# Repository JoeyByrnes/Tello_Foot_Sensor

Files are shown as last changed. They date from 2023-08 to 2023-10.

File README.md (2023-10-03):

# Tello Foot Sensor
Design Files and Firmware for an Ankle Encoder + Loadcell Amplifier Combo PCB for Tello Bipedal Robot

- STM32G4 Collects sensor data and streams over CAN-FD
- Position and velocity of the AS5147U encoder is read and streamed at 1KHz
- Two loadcells are read through two ADS1220 amplifiers and streamed at 1KHz
  - Optionally, four loadcells can be connected and streamed at ~700Hz

<p align="center">
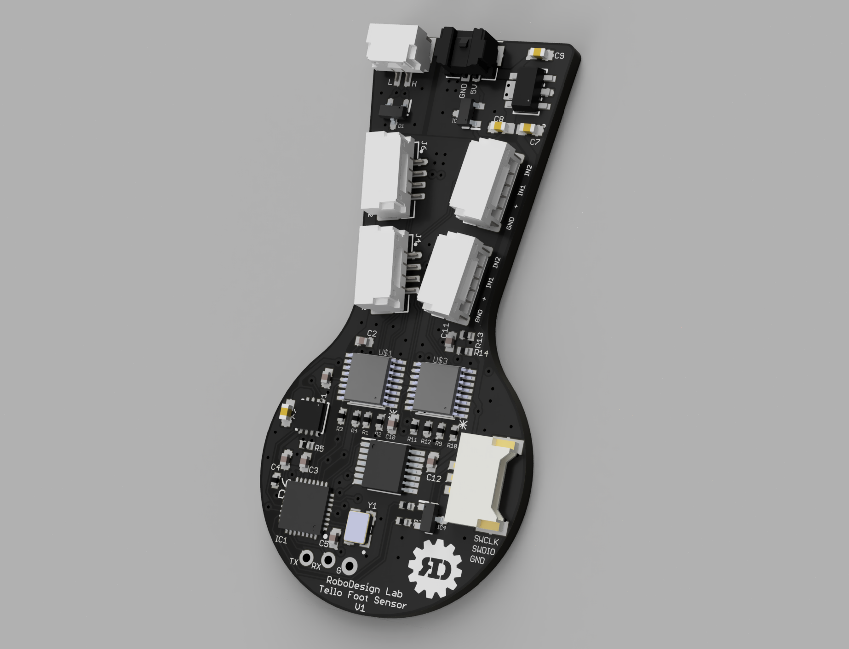
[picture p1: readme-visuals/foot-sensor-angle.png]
  
</p>
<p align="center">
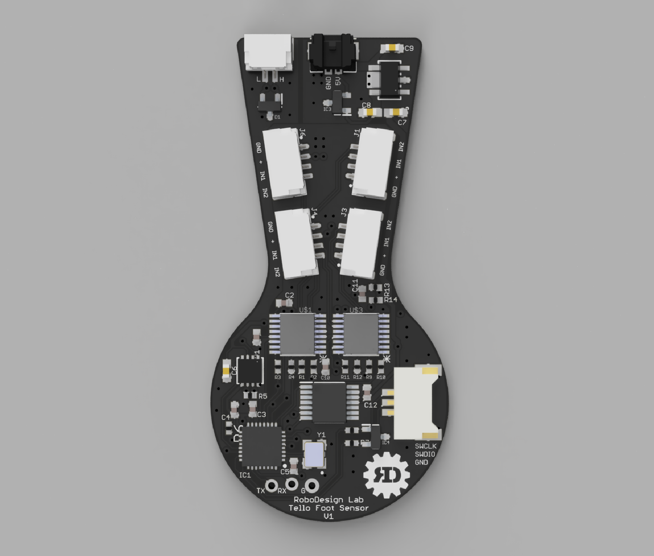
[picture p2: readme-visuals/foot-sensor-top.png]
  
</p>
<p align="center">
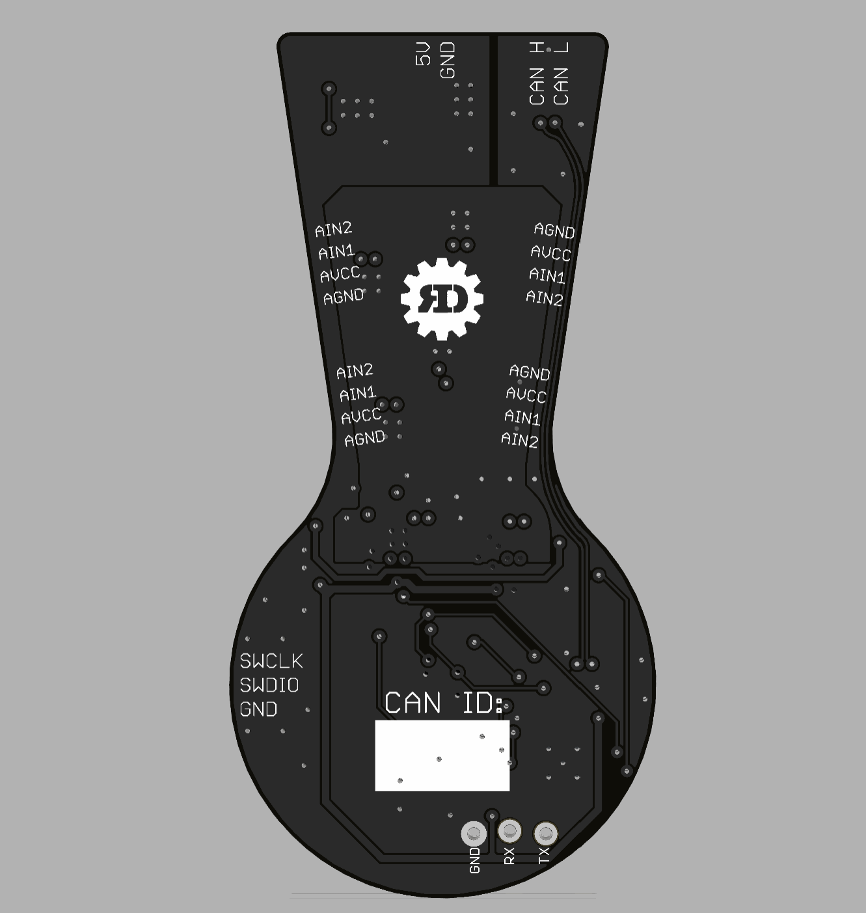
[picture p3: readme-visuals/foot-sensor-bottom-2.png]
  
</p>
<p align="center">
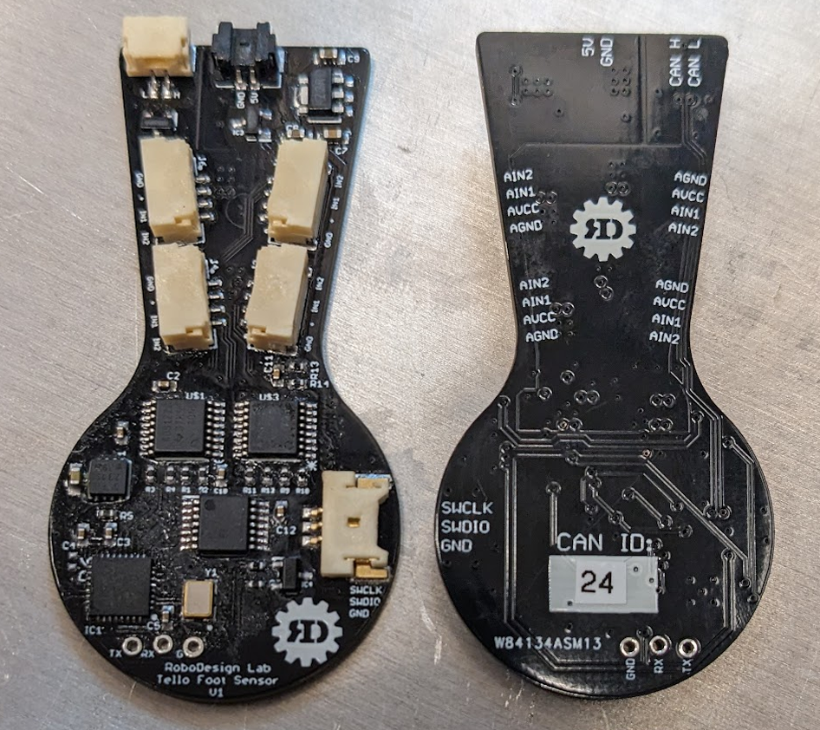
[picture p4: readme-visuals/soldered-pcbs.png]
  
</p>
<p align="center">
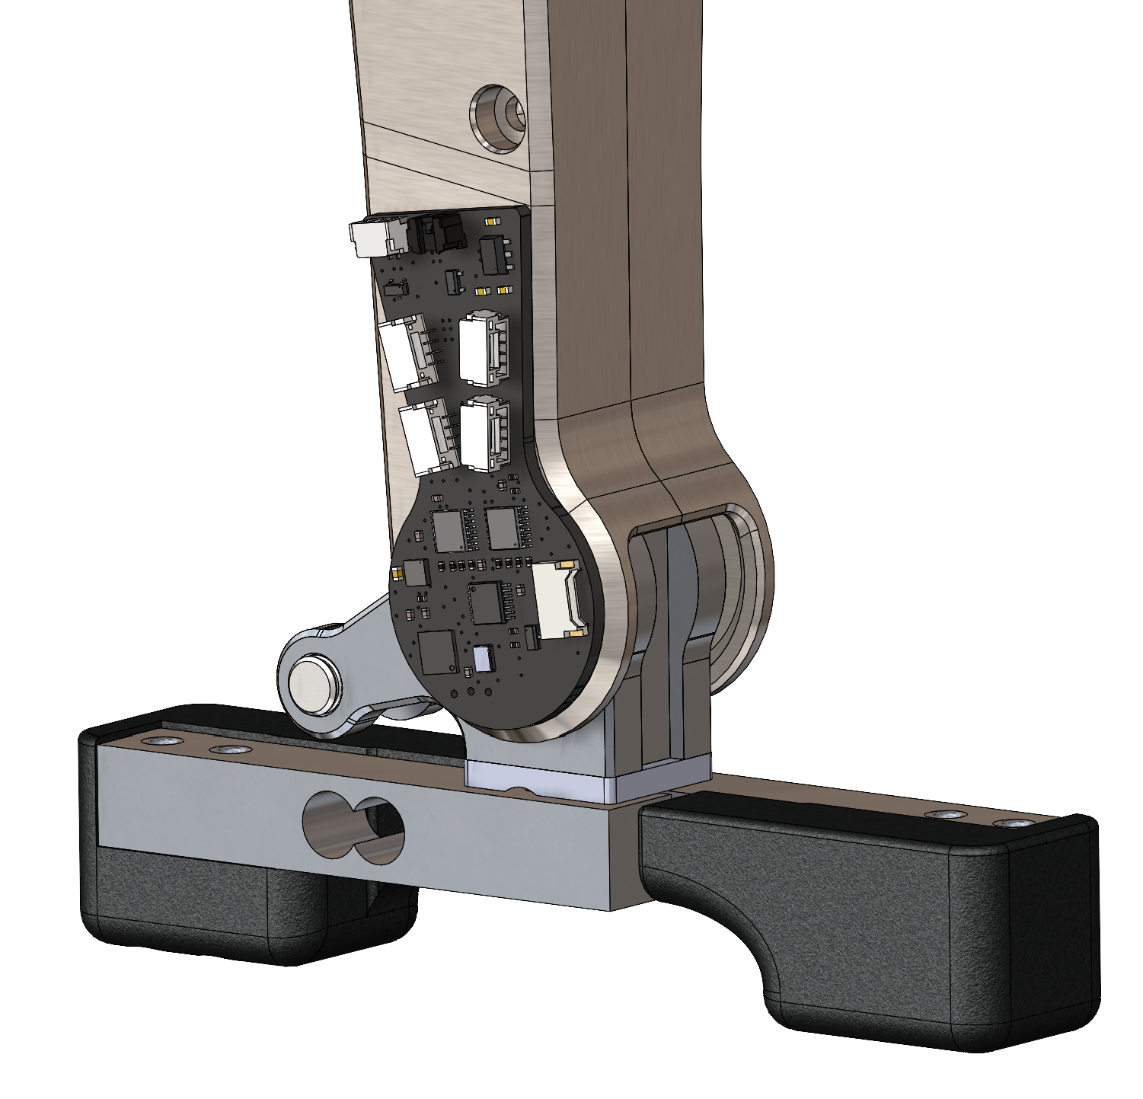
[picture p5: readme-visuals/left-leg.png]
  
</p>

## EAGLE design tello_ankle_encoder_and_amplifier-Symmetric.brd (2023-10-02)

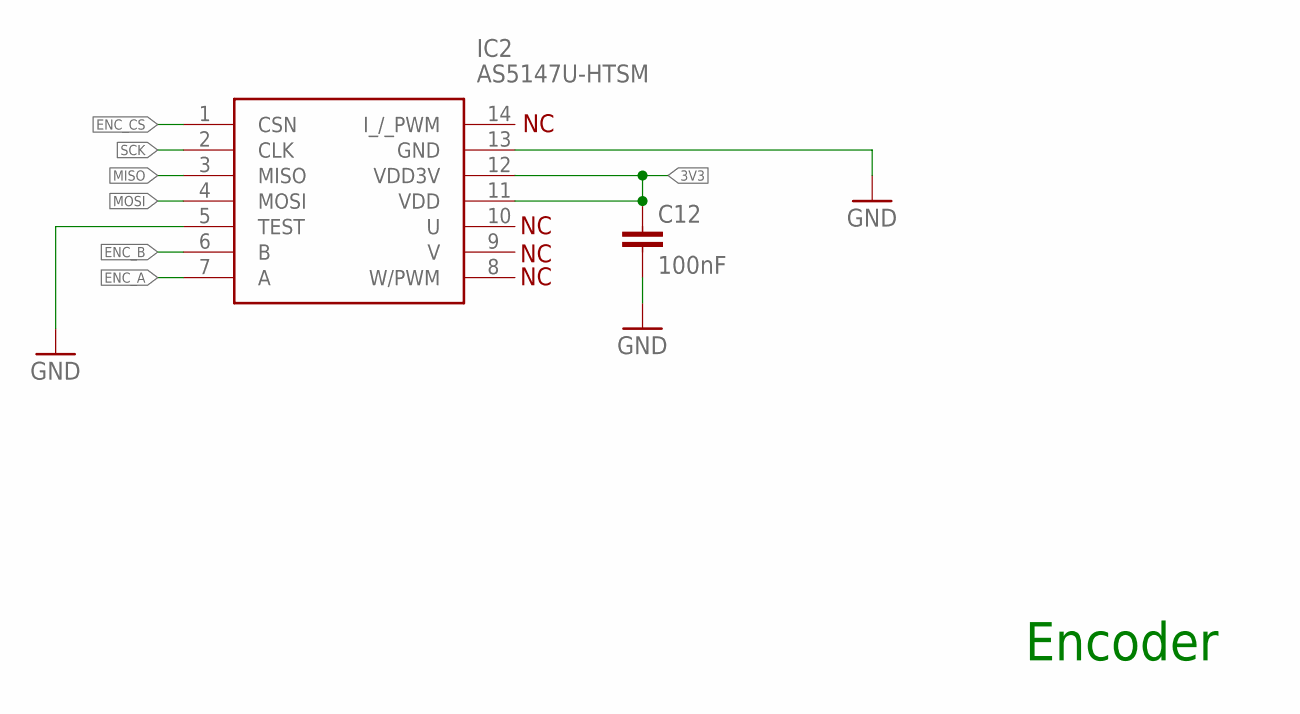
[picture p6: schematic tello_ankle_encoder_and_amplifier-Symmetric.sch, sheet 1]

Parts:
C12: 100nF; C0402
IC2: AS5147U-HTSM; SOP65P640X120-14N

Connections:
3V3: C12.1, IC2.11 (VDD), IC2.12 (VDD3V); also elsewhere on the board
ENC_A: IC2.7 (A); also elsewhere on the board
ENC_B: IC2.6 (B); also elsewhere on the board
ENC_CS: IC2.1 (CSN); also elsewhere on the board
GND: C12.2, IC2.5 (TEST), IC2.13 (GND); also elsewhere on the board
MISO: IC2.3 (MISO); also elsewhere on the board
MOSI: IC2.4 (MOSI); also elsewhere on the board
SCK: IC2.2 (CLK); also elsewhere on the board

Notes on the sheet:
Encoder

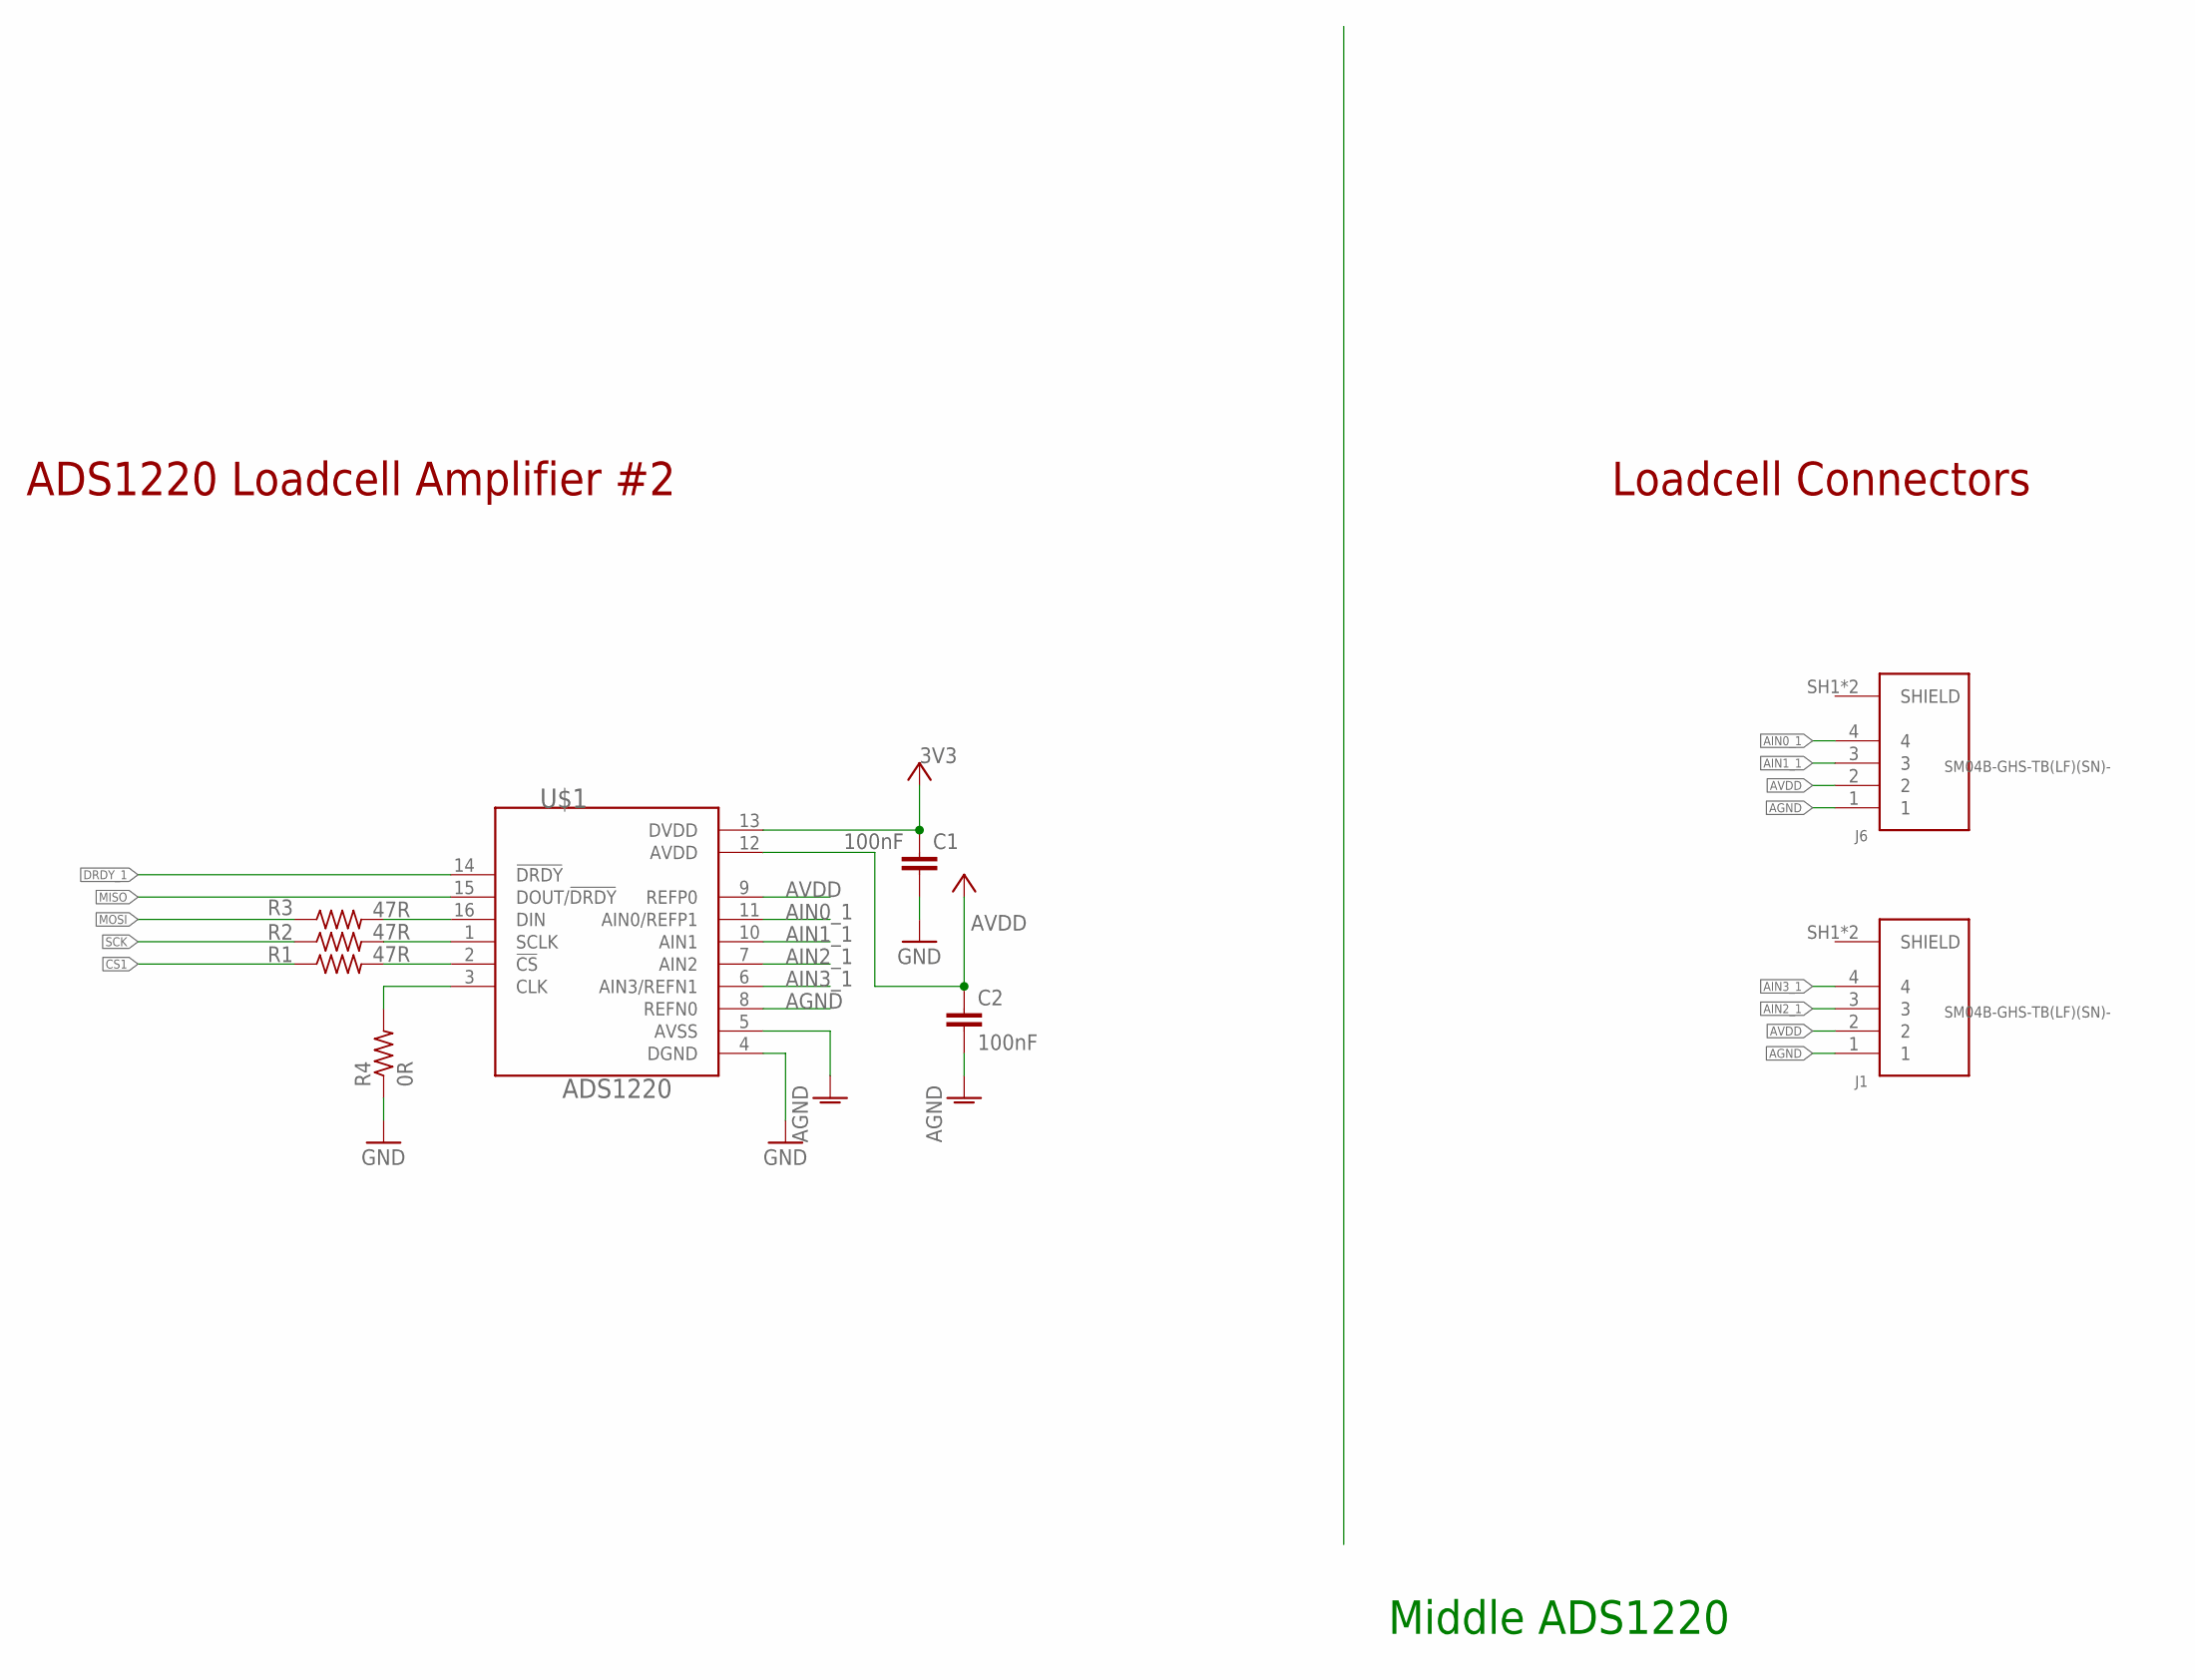
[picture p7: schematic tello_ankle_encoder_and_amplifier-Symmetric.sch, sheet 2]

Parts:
C1, C2: 100nF; C0402
J1, J6: SM04B-GHS-TB(LF)(SN)-; JST_SM04B-GHS-TB(LF)(SN)-
R1, R2, R3: 47R; R0402
R4: 0R; R0402
U$1: ADS1220; TSSOP-16

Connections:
3V3: C1.1, U$1.13 (DVDD); also elsewhere on the board
AGND: C2.2, J1.1, J6.1, U$1.5 (AVSS), U$1.8 (REFN0); also elsewhere on the board
AIN0_1: J6.4, U$1.11 (AIN0/REFP1)
AIN1_1: J6.3, U$1.10 (AIN1)
AIN2_1: J1.3, U$1.7 (AIN2)
AIN3_1: J1.4, U$1.6 (AIN3/REFN1)
AVDD: C2.1, J1.2, J6.2, U$1.9 (REFP0), U$1.12 (AVDD); also elsewhere on the board
CS1: R1.1; also elsewhere on the board
DRDY_1: U$1.14 (!DRDY); also elsewhere on the board
GND: C1.2, R4.1, U$1.4 (DGND); also elsewhere on the board
MISO: U$1.15 (DOUT/!DRDY); also elsewhere on the board
MOSI: R3.1; also elsewhere on the board
unnamed: R3.2, U$1.16 (DIN)
unnamed: R2.2, U$1.1 (SCLK)
unnamed: R1.2, U$1.2 (!CS)
unnamed: R4.2, U$1.3 (CLK)
SCK: R2.1; also elsewhere on the board
SHIELD: J1.SH1 (SHIELD), J1.SH2 (SHIELD), J6.SH1 (SHIELD), J6.SH2 (SHIELD); also elsewhere on the board

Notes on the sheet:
Middle ADS1220
ADS1220 Loadcell Amplifier #2
Loadcell Connectors

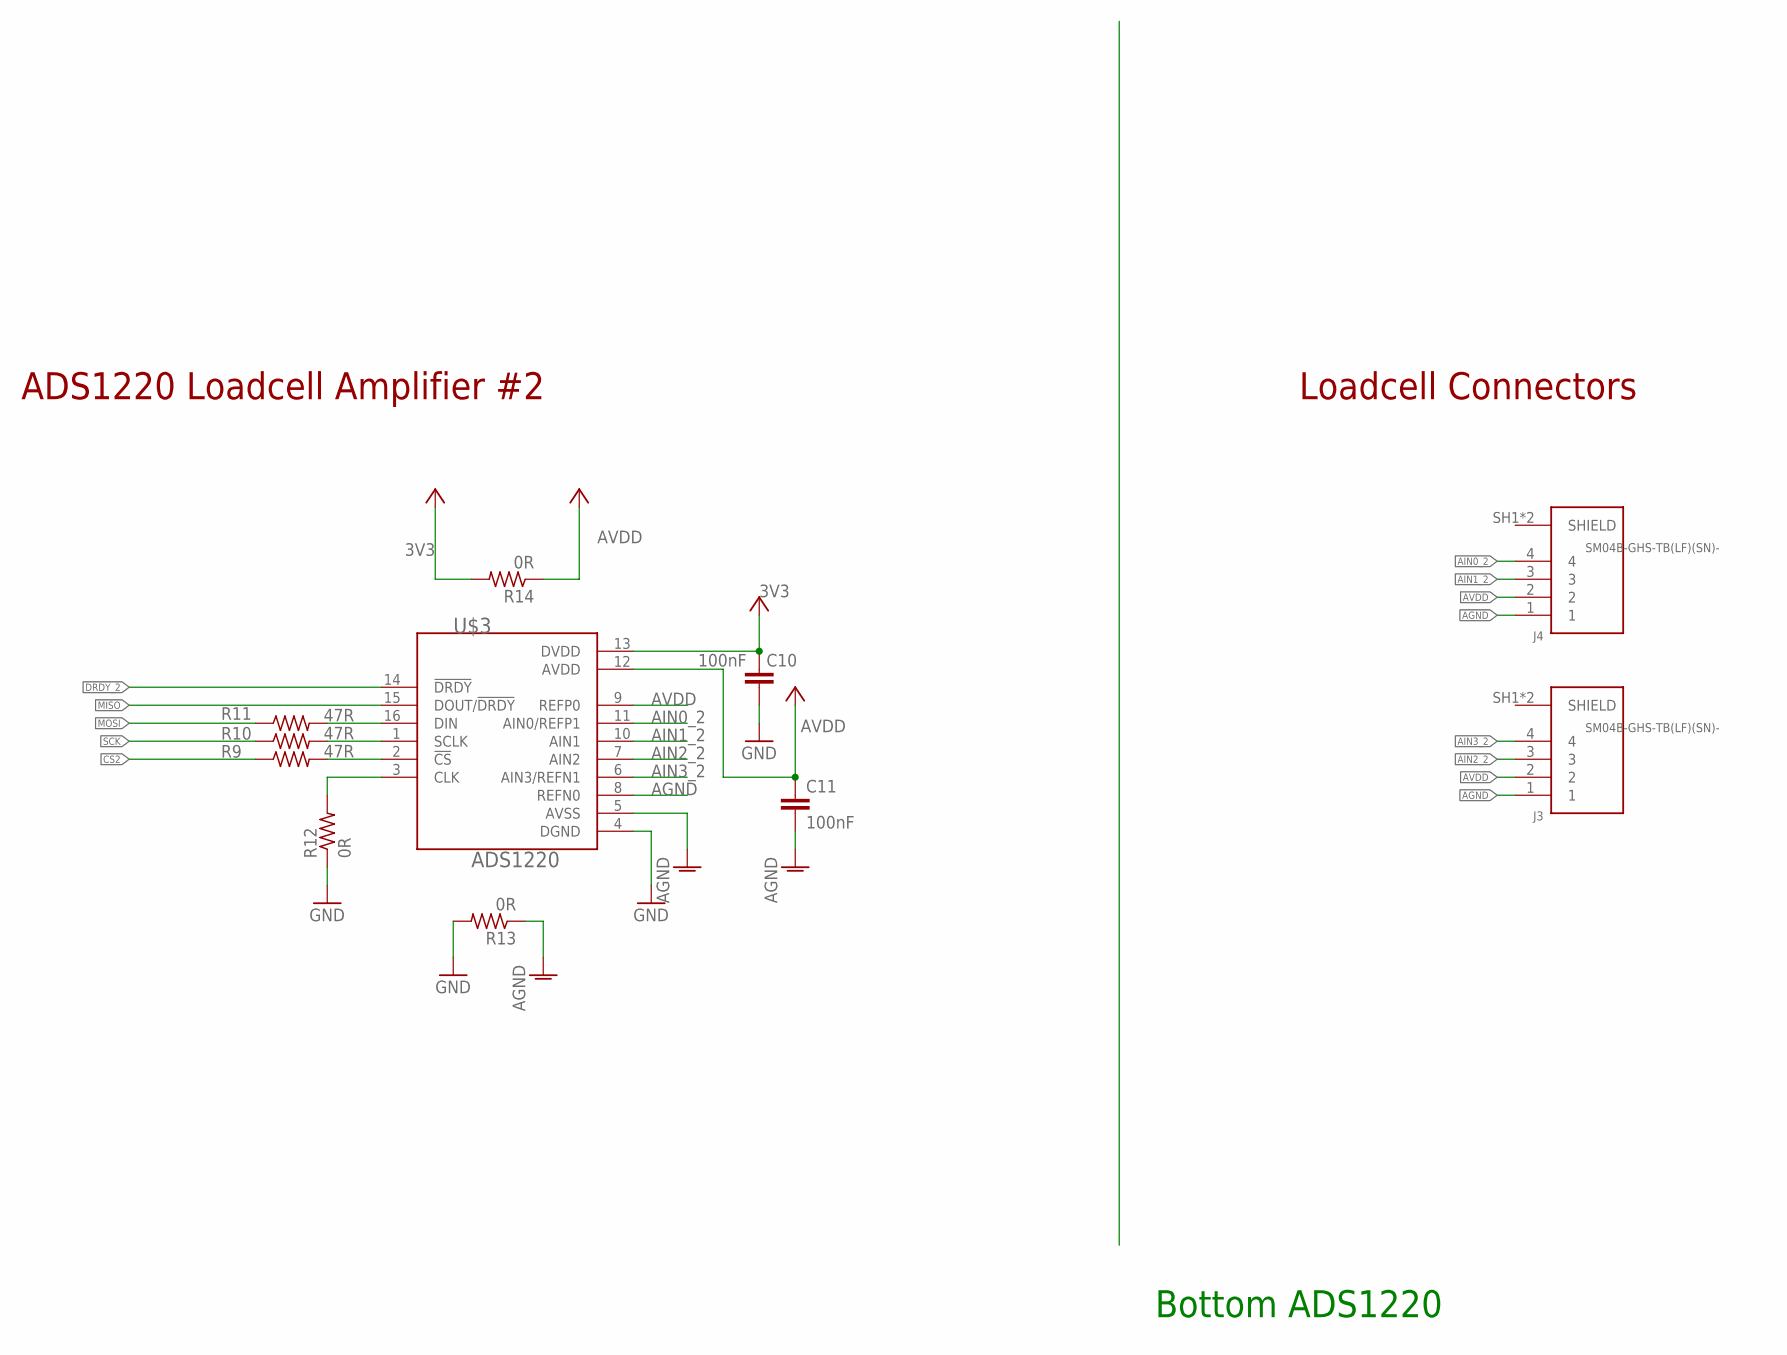
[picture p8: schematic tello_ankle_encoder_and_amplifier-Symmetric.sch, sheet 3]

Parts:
C10, C11: 100nF; C0402
J3, J4: SM04B-GHS-TB(LF)(SN)-; JST_SM04B-GHS-TB(LF)(SN)-
R9, R10, R11: 47R; R0402
R12, R13, R14: 0R; R0402
U$3: ADS1220; TSSOP-16

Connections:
3V3: C10.1, R14.2, U$3.13 (DVDD); also elsewhere on the board
AGND: C11.2, J3.1, J4.1, R13.1, U$3.5 (AVSS), U$3.8 (REFN0); also elsewhere on the board
AIN0_2: J4.4, U$3.11 (AIN0/REFP1)
AIN1_2: J4.3, U$3.10 (AIN1)
AIN2_2: J3.3, U$3.7 (AIN2)
AIN3_2: J3.4, U$3.6 (AIN3/REFN1)
AVDD: C11.1, J3.2, J4.2, R14.1, U$3.9 (REFP0), U$3.12 (AVDD); also elsewhere on the board
CS2: R9.1; also elsewhere on the board
DRDY_2: U$3.14 (!DRDY); also elsewhere on the board
GND: C10.2, R12.1, R13.2, U$3.4 (DGND); also elsewhere on the board
MISO: U$3.15 (DOUT/!DRDY); also elsewhere on the board
MOSI: R11.1; also elsewhere on the board
unnamed: R11.2, U$3.16 (DIN)
unnamed: R10.2, U$3.1 (SCLK)
unnamed: R9.2, U$3.2 (!CS)
unnamed: R12.2, U$3.3 (CLK)
SCK: R10.1; also elsewhere on the board
SHIELD: J3.SH1 (SHIELD), J3.SH2 (SHIELD), J4.SH1 (SHIELD), J4.SH2 (SHIELD); also elsewhere on the board

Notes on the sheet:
Bottom ADS1220
ADS1220 Loadcell Amplifier #2
Loadcell Connectors

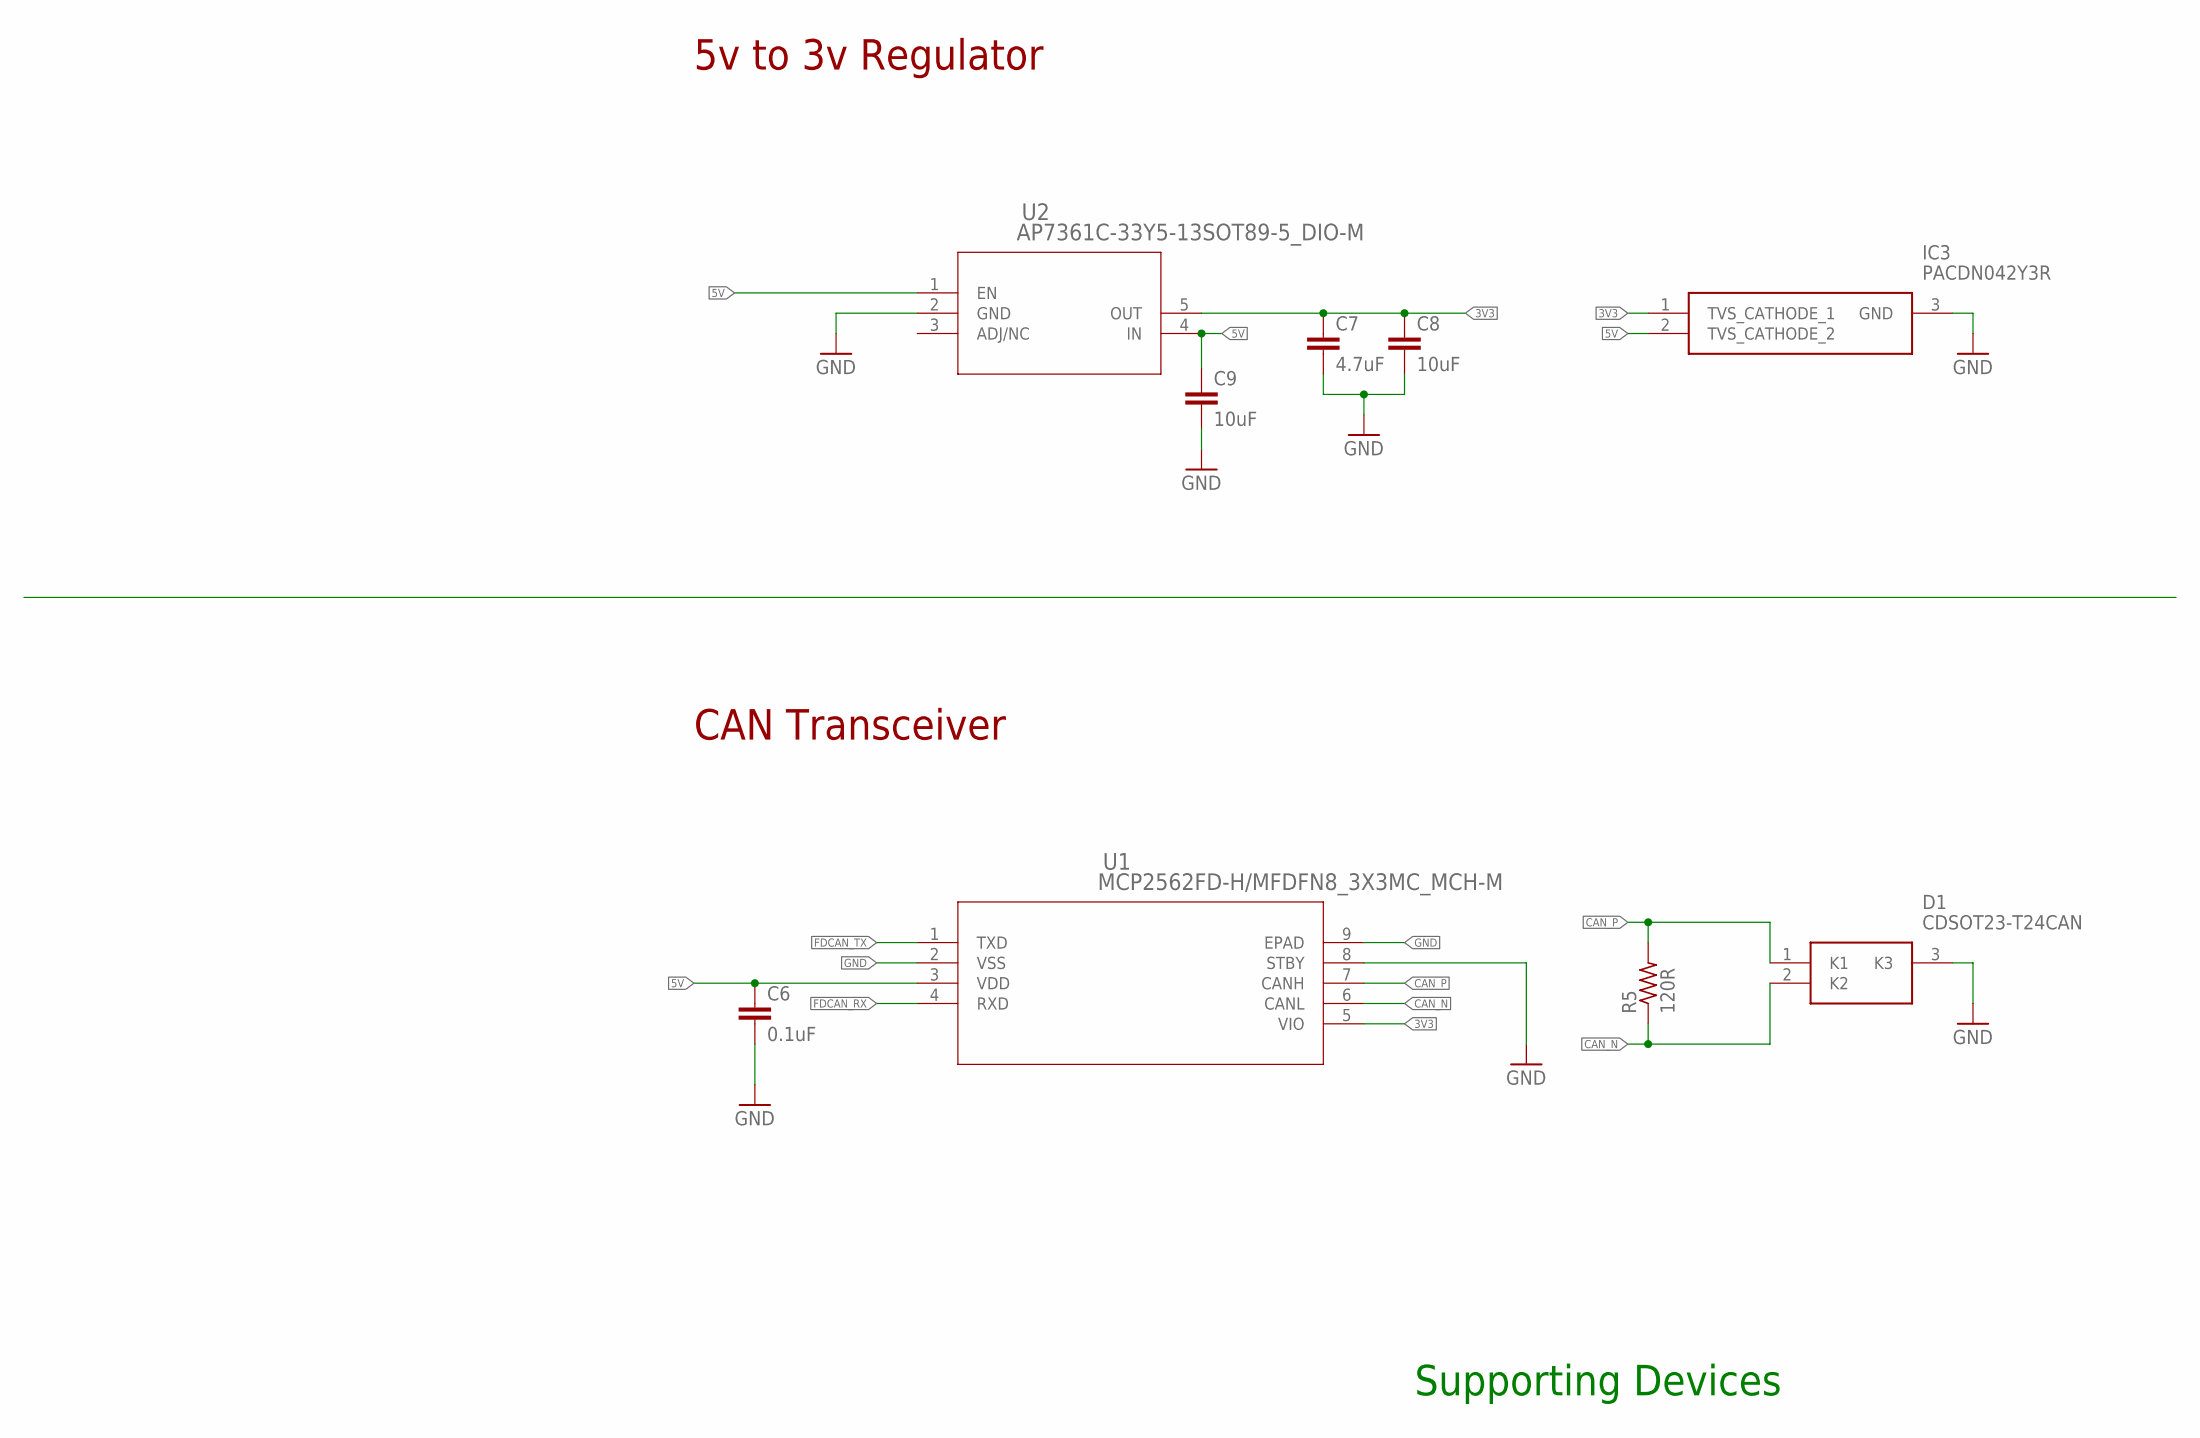
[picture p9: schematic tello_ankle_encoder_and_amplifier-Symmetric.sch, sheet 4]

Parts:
C6: 0.1uF; C0603
C7: 4.7uF; C0603
C8, C9: 10uF; C0603
D1: CDSOT23-T24CAN; SOT95P230X117-3N
IC3: PACDN042Y3R; SOT96P237X111-3N
R5: 120R; R0402
U1: MCP2562FD-H/MFDFN8_3X3MC_MCH-M; DFN8_3X3MC_MCH-M
U2: AP7361C-33Y5-13SOT89-5_DIO-M; SOT89-5_DIO-M

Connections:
3V3: C7.1, C8.1, IC3.1 (TVS_CATHODE_1), U1.5 (VIO), U2.5 (OUT); also elsewhere on the board
5V: C6.1, C9.1, IC3.2 (TVS_CATHODE_2), U1.3 (VDD), U2.1 (EN), U2.4 (IN); also elsewhere on the board
CAN_N: D1.2 (K2), R5.1, U1.6 (CANL); also elsewhere on the board
CAN_P: D1.1 (K1), R5.2, U1.7 (CANH); also elsewhere on the board
FDCAN_RX: U1.4 (RXD); also elsewhere on the board
FDCAN_TX: U1.1 (TXD); also elsewhere on the board
GND: C6.2, C7.2, C8.2, C9.2, D1.3 (K3), IC3.3 (GND), U1.2 (VSS), U1.8 (STBY), U1.9 (EPAD), U2.2 (GND); also elsewhere on the board

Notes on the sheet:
5v to 3v Regulator
CAN Transceiver
Supporting Devices

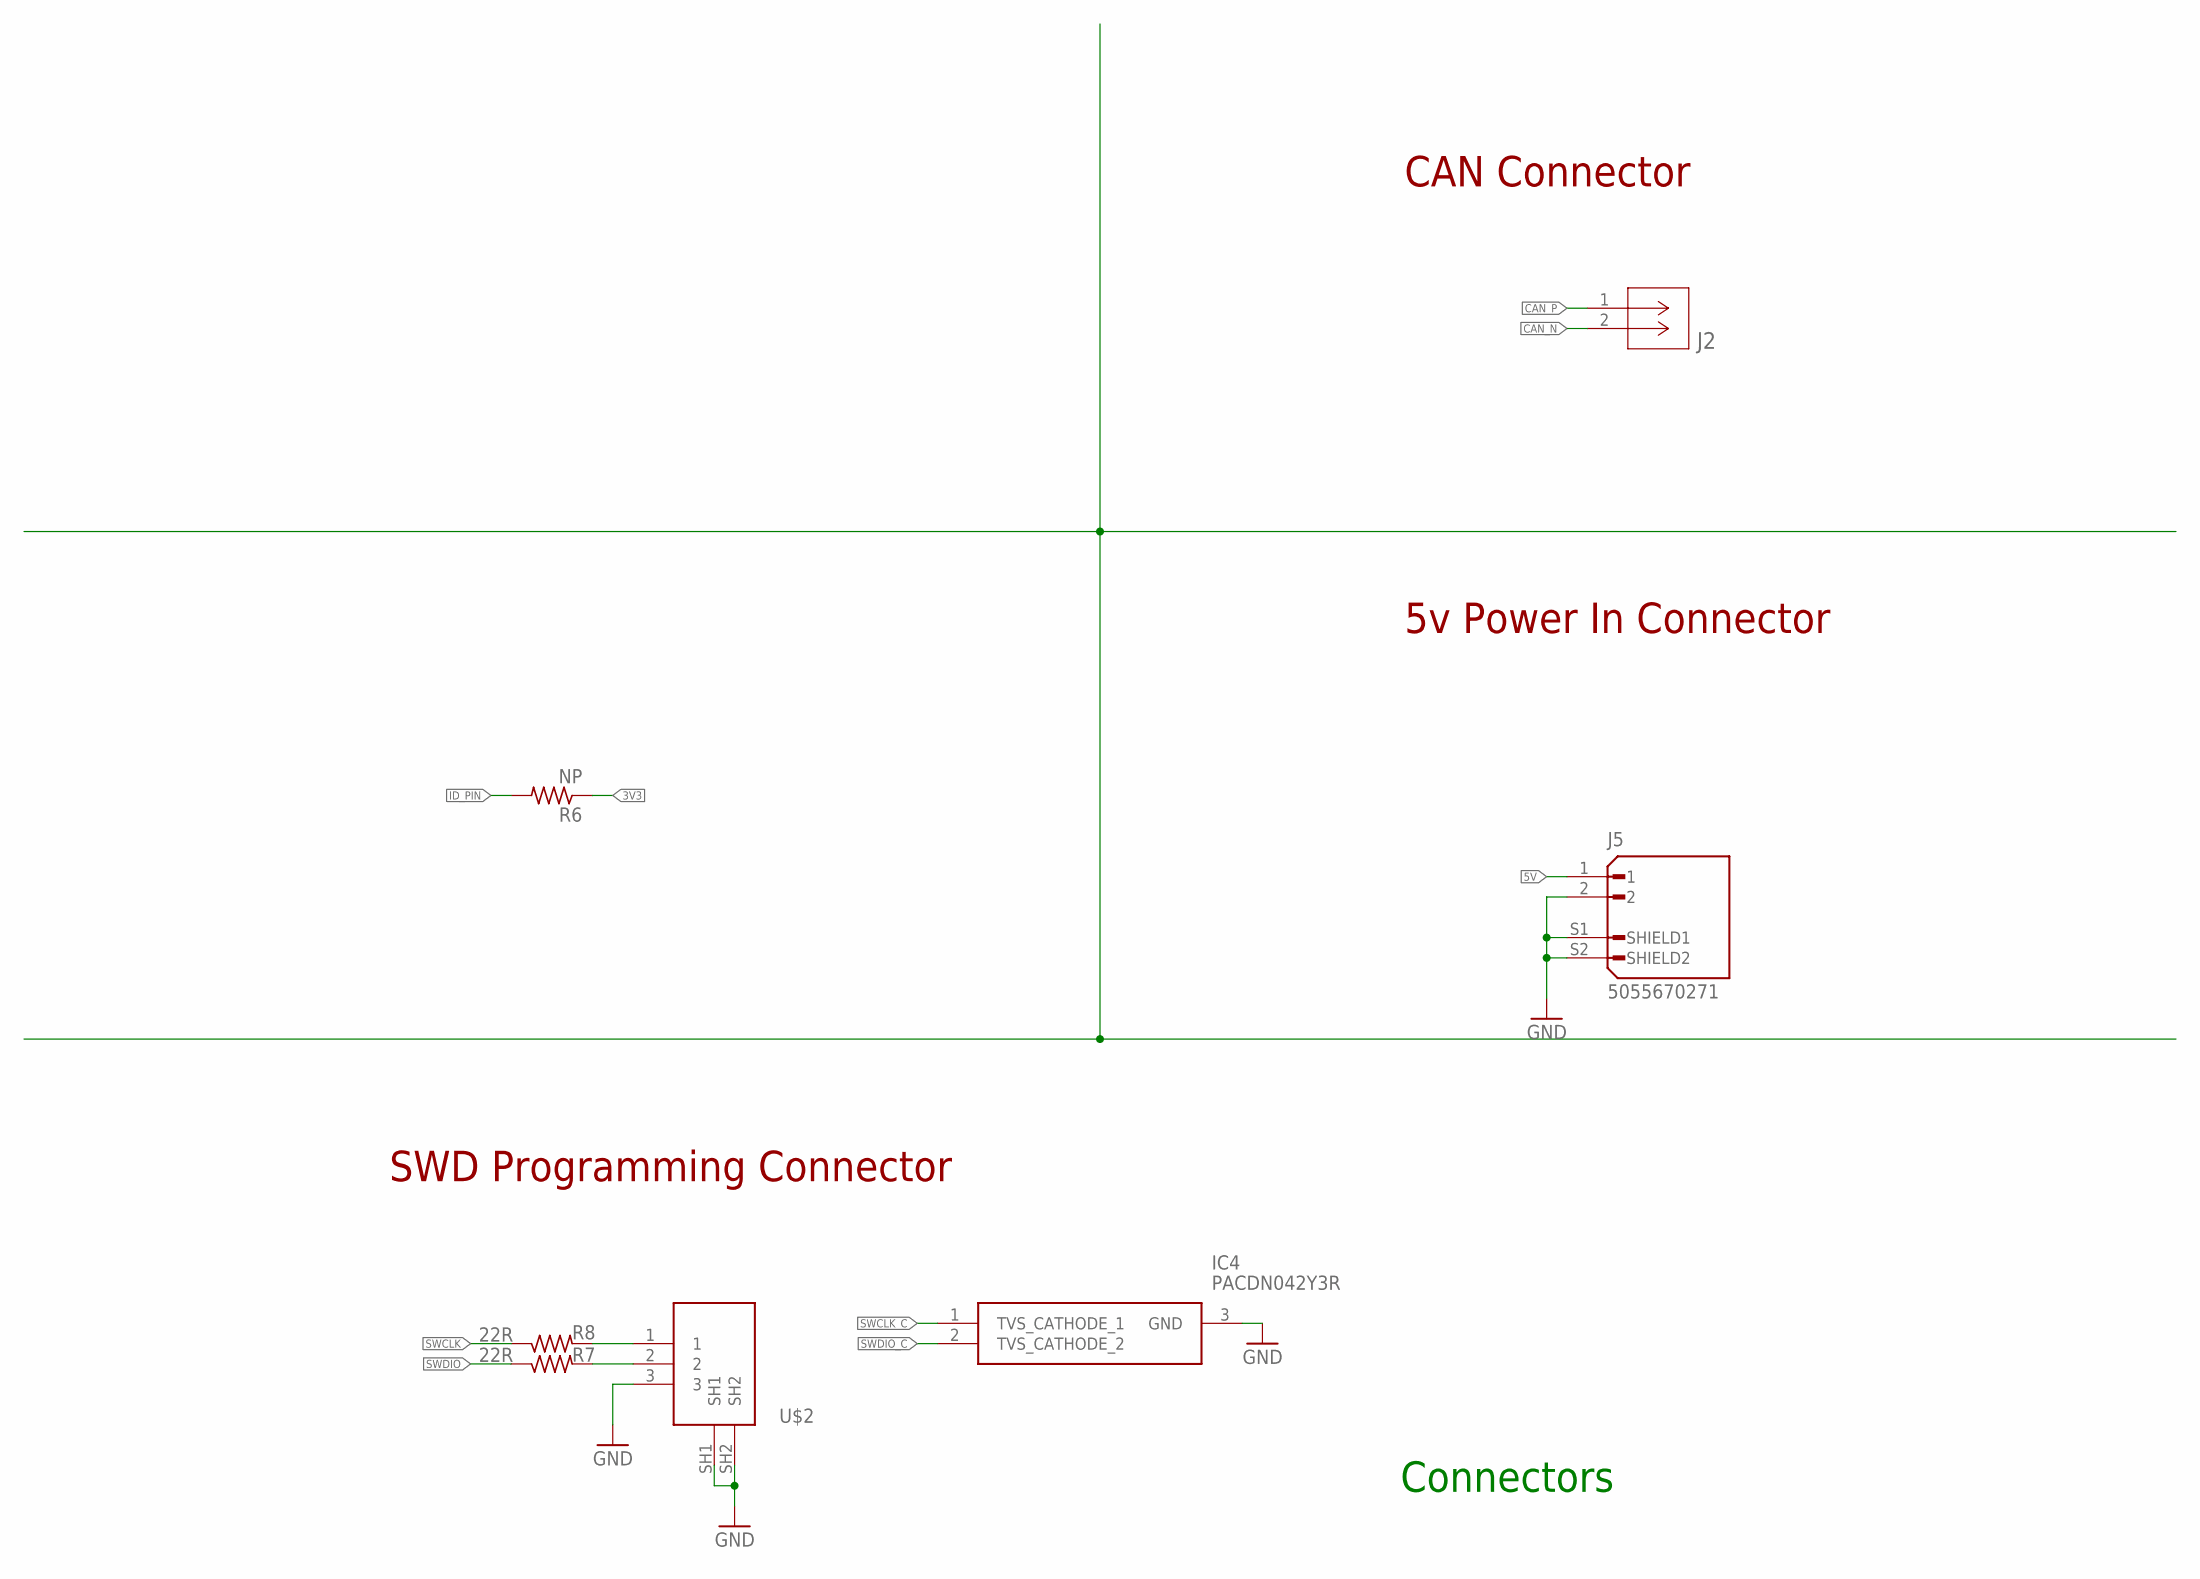
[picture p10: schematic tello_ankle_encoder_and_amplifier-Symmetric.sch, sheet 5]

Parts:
IC4: PACDN042Y3R; SOT96P237X111-3N
J2: SM02BGHSTBLFSN; CONN_SM02BGHSTB_JST
J5: 5055670271; MOLEX_5055670271
R6: NP; R0402
R7, R8: 22R; R0402
U$2: 125SH-G-03-TR-SMT

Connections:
3V3: R6.1; also elsewhere on the board
5V: J5.1; also elsewhere on the board
CAN_N: J2.2; also elsewhere on the board
CAN_P: J2.1; also elsewhere on the board
GND: IC4.3 (GND), J5.2, J5.S1 (SHIELD1), J5.S2 (SHIELD2), U$2.3, U$2.SH1, U$2.SH2; also elsewhere on the board
ID_PIN: R6.2; also elsewhere on the board
SWCLK: R8.1; also elsewhere on the board
SWCLK_C: IC4.1 (TVS_CATHODE_1), R8.2, U$2.1
SWDIO: R7.1; also elsewhere on the board
SWDIO_C: IC4.2 (TVS_CATHODE_2), R7.2, U$2.2

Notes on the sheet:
U$2
CAN Connector
5v Power In Connector
SWD Programming Connector
Connectors

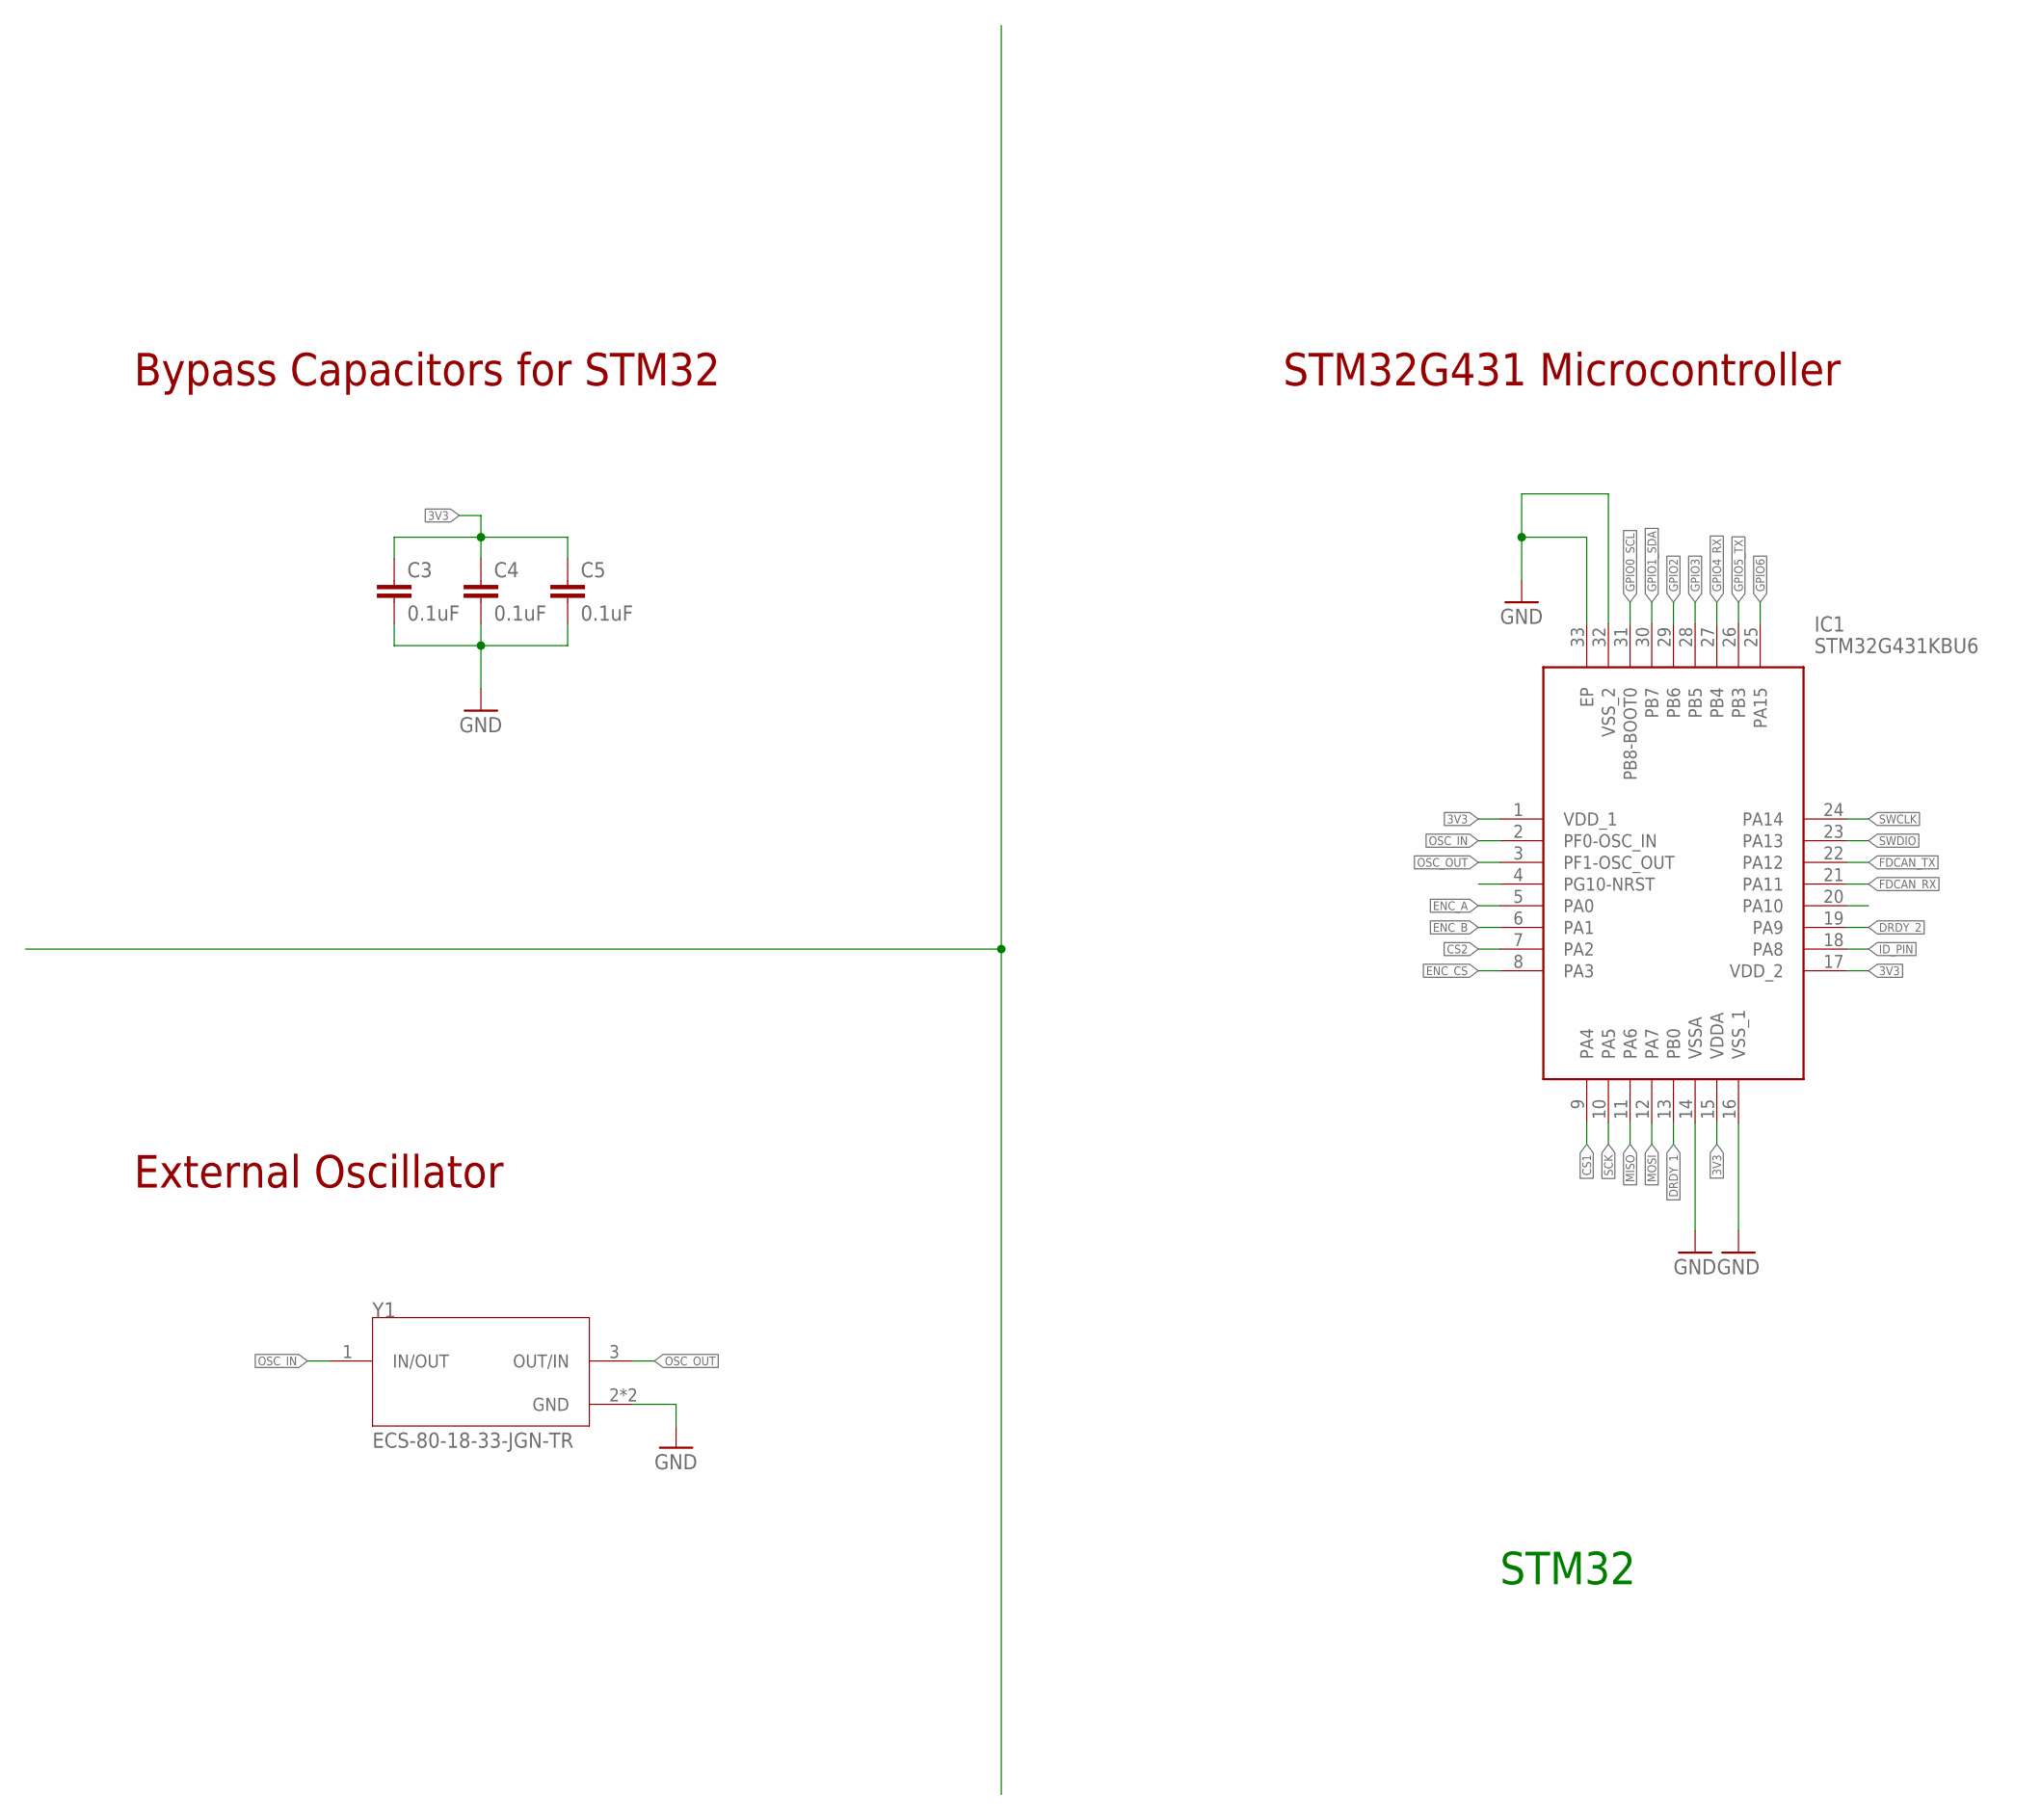
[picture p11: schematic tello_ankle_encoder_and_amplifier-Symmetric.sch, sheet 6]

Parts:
C3, C4, C5: 0.1uF; C0402
IC1: STM32G431KBU6; QFN50P500X500X60-33N
Y1: ECS-80-18-33-JGN-TR; XTAL_ECS-240-8-33-AGN-TR

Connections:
3V3: C3.1, C4.1, C5.1, IC1.1 (VDD_1), IC1.15 (VDDA), IC1.17 (VDD_2); also elsewhere on the board
CS1: IC1.9 (PA4); also elsewhere on the board
CS2: IC1.7 (PA2); also elsewhere on the board
DRDY_1: IC1.13 (PB0); also elsewhere on the board
DRDY_2: IC1.19 (PA9); also elsewhere on the board
ENC_A: IC1.5 (PA0); also elsewhere on the board
ENC_B: IC1.6 (PA1); also elsewhere on the board
ENC_CS: IC1.8 (PA3); also elsewhere on the board
FDCAN_RX: IC1.21 (PA11); also elsewhere on the board
FDCAN_TX: IC1.22 (PA12); also elsewhere on the board
GND: C3.2, C4.2, C5.2, IC1.14 (VSSA), IC1.16 (VSS_1), IC1.32 (VSS_2), IC1.33 (EP), Y1.2 (GND), Y1.4 (GND); also elsewhere on the board
GPIO0_SCL: IC1.31 (PB8-BOOT0)
GPIO1_SDA: IC1.30 (PB7)
GPIO2: IC1.29 (PB6)
GPIO3: IC1.28 (PB5)
GPIO4_RX: IC1.27 (PB4)
GPIO5_TX: IC1.26 (PB3)
GPIO6: IC1.25 (PA15)
ID_PIN: IC1.18 (PA8); also elsewhere on the board
MISO: IC1.11 (PA6); also elsewhere on the board
MOSI: IC1.12 (PA7); also elsewhere on the board
OSC_IN: IC1.2 (PF0-OSC_IN), Y1.1 (IN/OUT)
OSC_OUT: IC1.3 (PF1-OSC_OUT), Y1.3 (OUT/IN)
SCK: IC1.10 (PA5); also elsewhere on the board
SWCLK: IC1.24 (PA14); also elsewhere on the board
SWDIO: IC1.23 (PA13); also elsewhere on the board

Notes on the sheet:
Bypass Capacitors for STM32
External Oscillator
STM32G431 Microcontroller
STM32

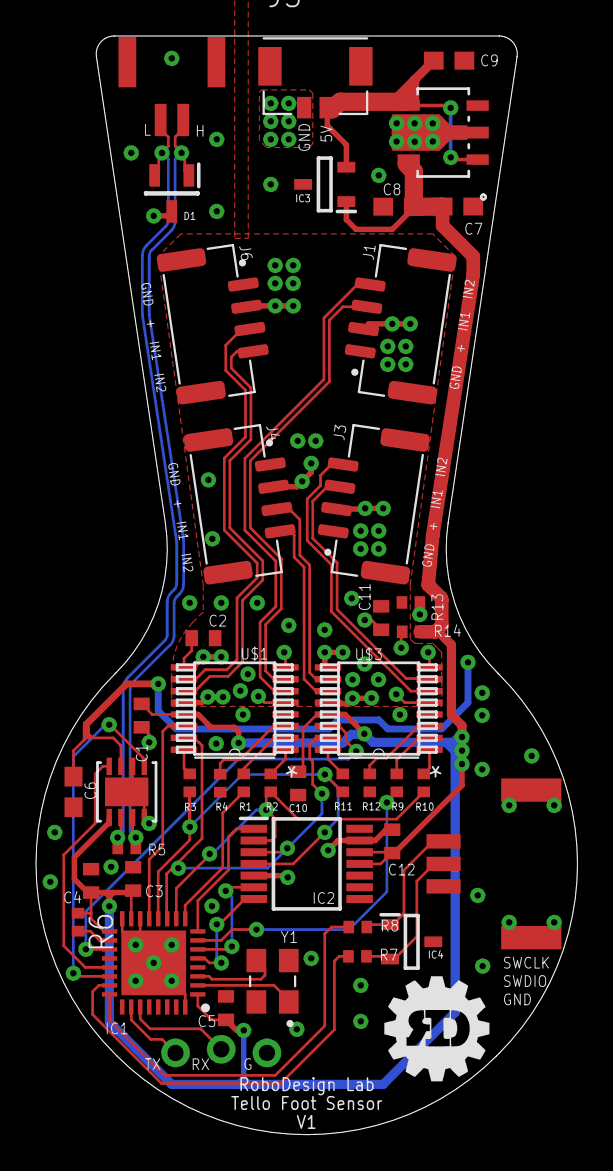
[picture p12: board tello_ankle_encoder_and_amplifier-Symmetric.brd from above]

Board: 4 copper layers, 30.1 x 61.0 mm, 43 parts (0 on the bottom side), 43 nets.

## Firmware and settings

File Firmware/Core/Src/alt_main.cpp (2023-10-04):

#include <dwt_delay.hpp>
#include "alt_main.h"
#include "stm32g4xx_hal.h"
#include <Protocentral_ADS1220.hpp>
#include <string.h>
#include <stdio.h>
#include "main.h"
#include <math.h>

#define CPU_FREQ_HZ (float)170e6

#define AS4047D_CS1_Port GPIOA
#define AS4047D_CS1_Pin GPIO_PIN_3
#define ENC_CS_HIGH AS4047D_CS1_Port->BSRR=(uint32_t)AS4047D_CS1_Pin
#define ENC_CS_LOW AS4047D_CS1_Port->BRR=(uint32_t)AS4047D_CS1_Pin
#define READ_POS_REG 0xFFFF
#define READ_POS_REG_COMP 0xFFFE
#define READ_VEL_REG 0xFFFC

#define HALF_ENC_CPR 8192

//#define CAN_DEVICE_ID_ENC (THIS IS UNUSED NOW, ID is read from FLASH)
#define CAN_DEVICE_ID_ENC_ADDRESS ((uint8_t*)0x0800FFF0)
#define CAN_MASTER_ID (uint8_t)0
#define CAN_DATA_SIZE 8    // Number of data bytes in a CAN packet

uint8_t encoder_packet[8]; // Packet 1 with 8 bytes

FDCAN_TxHeaderTypeDef txHeader;

uint8_t can_id = 0;

uint16_t last_raw_pos = 0;
int num_turns = 0;

union FloatToBytes {
    float f;
    uint8_t b[sizeof(float)];
};

union Int32ToBytes {
    int32_t i;
    uint8_t b[sizeof(int32_t)];
};

union Int16ToBytes {
    int16_t i;
    uint8_t b[sizeof(int16_t)];
};


bool first_reading = true;

extern UART_HandleTypeDef huart2;

extern SPI_HandleTypeDef hspi1;

extern DMA_HandleTypeDef hdma_usart2_tx;

extern FDCAN_HandleTypeDef hfdcan1;


uint16_t AS5147_Read_Pos()
{
	ENC_CS_LOW;
	while ((SPI1->SR & SPI_SR_BSY) != 0);
	SPI1->DR = READ_POS_REG;
	SPI1->CR1 |= SPI_CR1_SPE;
	while ((SPI1->SR & SPI_SR_RXNE) == 0);
	uint16_t result = SPI1->DR;
	while ((SPI1->SR & SPI_SR_TXE) == 0);
	while ((SPI1->SR & SPI_SR_BSY) != 0);
	SPI1->CR1 &= ~(SPI_CR1_SPE);
	ENC_CS_HIGH;
	return (result & 0x3FFF);
}

uint16_t AS5147_Read_Vel()
{
	ENC_CS_LOW;
	while ((SPI1->SR & SPI_SR_BSY) != 0);
	SPI1->DR = READ_VEL_REG;
	SPI1->CR1 |= SPI_CR1_SPE;
	while ((SPI1->SR & SPI_SR_RXNE) == 0);
	uint16_t result = SPI1->DR;
	while ((SPI1->SR & SPI_SR_TXE) == 0);
	while ((SPI1->SR & SPI_SR_BSY) != 0);
	SPI1->CR1 &= ~(SPI_CR1_SPE);
	ENC_CS_HIGH;
	return (result & 0x3FFF);
}

int32_t twoscomp14bit_to_int(int16_t value) {
    // Extract the sign bit from the 14-bit number (bit 13)
    int32_t sign_bit = (value & 0x2000) ? 0xFFFFC000 : 0x00000000;

    // Extend the 14-bit number to 32 bits while preserving its sign
    int32_t result = (int32_t)(value | sign_bit);

    return result;
}


int alt_main()
{
	/* Initialization */
	can_id = *(CAN_DEVICE_ID_ENC_ADDRESS);

	txHeader.Identifier = (can_id-20); // will set master IDs to 0 through 9 to avoid conflicts
	txHeader.IdType = FDCAN_STANDARD_ID;
	txHeader.TxFrameType = FDCAN_DATA_FRAME;
	txHeader.DataLength = FDCAN_DLC_BYTES_8;
	txHeader.ErrorStateIndicator = FDCAN_ESI_ACTIVE;
	txHeader.BitRateSwitch = FDCAN_BRS_OFF;
	txHeader.FDFormat = FDCAN_CLASSIC_CAN;
	txHeader.TxEventFifoControl = FDCAN_NO_TX_EVENTS;
	txHeader.MessageMarker = 0;

	last_raw_pos = AS5147_Read_Pos();



	while (1)
	{


	}
}

int serial_cnt = 0;

void setSPIMode(int mode)
{
	SPI1->CR1 &= ~SPI_CR1_SPE;
	if(mode == 1){
		// Set CPOL and CPHA bits to configure SPI mode 1
		SPI1->CR1 &= ~SPI_CR1_CPOL;  // Clear CPOL bit (CPOL = 0)
		SPI1->CR1 |= SPI_CR1_CPHA;   // Set CPHA bit  (CPHA = 1)
	}
	else if(mode == 0){
		// Set CPOL and CPHA bits to configure SPI mode 1
		SPI1->CR1 &= ~SPI_CR1_CPOL;  // Clear CPOL bit (CPOL = 0)
		SPI1->CR1 &= ~SPI_CR1_CPHA;   // Set CPHA bit  (CPHA = 0)
	}
	SPI1->CR1 |= SPI_CR1_SPE;
}

void main_1KHz_interrupt()
{

	int multiturn_pos;

	AS5147_Read_Pos();
	AS5147_Read_Pos();
	uint16_t pos = AS5147_Read_Pos();

	int rollover = 0;
	int angle_diff = pos - last_raw_pos;
	if(angle_diff > HALF_ENC_CPR){rollover = -1;}
	else if(angle_diff < -HALF_ENC_CPR){rollover = 1;}
	num_turns += rollover;

	/* Multi-turn position */
	multiturn_pos = pos + 16384*num_turns;

	last_raw_pos = pos;

	AS5147_Read_Vel();
	AS5147_Read_Vel();
	uint16_t velEnc = AS5147_Read_Vel();


	int velInt = twoscomp14bit_to_int(velEnc);


//	FloatToBytes velf2b;
//	velf2b.f = velocity;
	Int32ToBytes int2b;
	int2b.i = velInt;

	// ================================================================================================

	txHeader.DataLength = FDCAN_DLC_BYTES_8;

	encoder_packet[0] = can_id;
	encoder_packet[1] = (pos >> 8) & 0xFF;
	encoder_packet[2] = (pos) & 0xFF;
	encoder_packet[3] = (127+num_turns) &0xFF; // turn tracking only supported up to 127 turns
	encoder_packet[4] = int2b.b[3];
	encoder_packet[5] = int2b.b[2];
	encoder_packet[6] = int2b.b[1];
	encoder_packet[7] = int2b.b[0];

	HAL_FDCAN_AddMessageToTxFifoQ(&hfdcan1, &txHeader, encoder_packet);
	usleep(200);

	char uartTxBuffer[1024];

	if(serial_cnt%100 == 0){
		sprintf(uartTxBuffer, "multiturn: %d,      velocity: %d    \r\n", multiturn_pos, velInt);
		HAL_UART_Transmit(&huart2, (uint8_t *)uartTxBuffer, strlen(uartTxBuffer),1);
	}
	serial_cnt++;


}

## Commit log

2023-08-16 board reviewed once
    [tello_ankle_encoder_and_amplifier-Symmetric.brd, tello_ankle_encoder_and_amplifier-Symmetric.sch]
2023-10-02 added manufacturing files
    [tello_ankle_encoder_and_amplifier-Symmetric.brd, tello_ankle_encoder_and_amplifier-Symmetric.sch]

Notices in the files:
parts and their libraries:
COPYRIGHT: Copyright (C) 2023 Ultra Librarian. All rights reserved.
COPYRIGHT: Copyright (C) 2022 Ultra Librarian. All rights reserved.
